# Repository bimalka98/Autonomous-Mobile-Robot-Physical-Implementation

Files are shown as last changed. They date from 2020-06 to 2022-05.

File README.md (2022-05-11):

## *Introduction*

This repository includes all the project files related to the development of an `Arduino based autonomous mobile robot`. The project is being done by a team of 5 undergraduates at the Department of Electronic and Telecommunication Engineering, University of Moratuwa, Sri Lanka. The following figures illustrates the `initial prototypes` of the planned mobile robot design and it may be subjected to various changes during the actual robot implementing stage due to possible reasons.

|*Version 1*|*Version 2*|
|:----:|:----:|
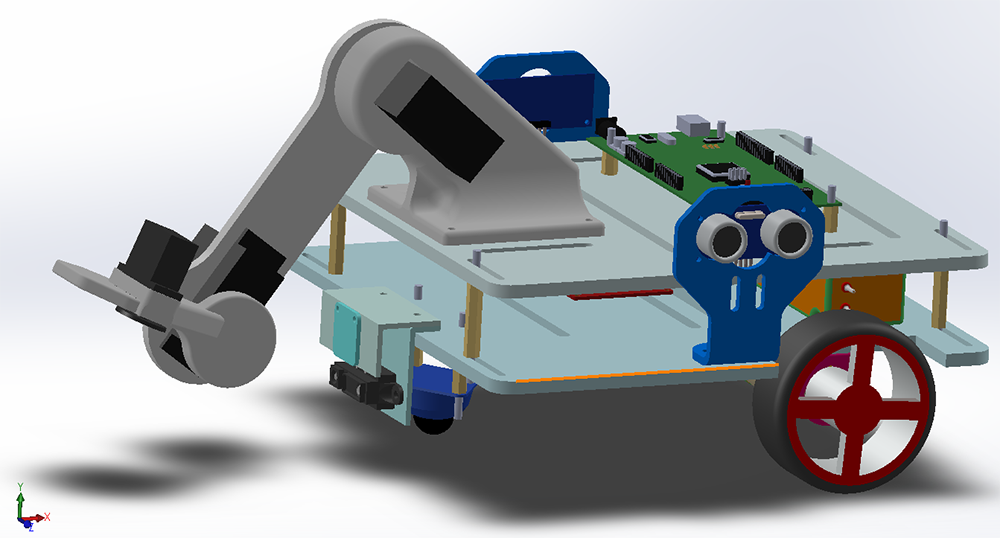
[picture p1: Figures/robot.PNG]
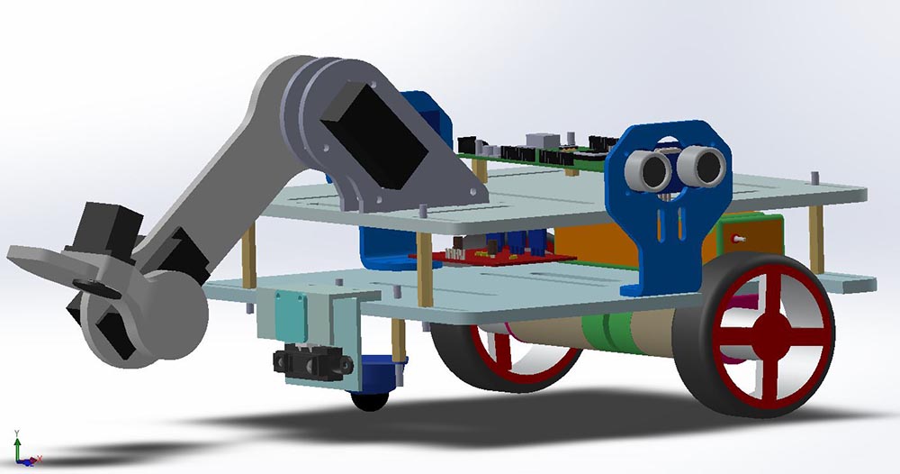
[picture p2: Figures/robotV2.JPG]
||  |

---

## *Current Status of the Project*

* Algorithms were developed.
* Working on coding.
* Physical Robot building stage was initialized.
* Robot arm's basic motion was implemented.
* Line following algirithm is being debugged.

---

## *Brief introduction about the files in repository*

### LatestStable
This folder contains the latest stable version of the Arduino code tested and debugged by the team.

### Arduino Sketches
This folder contains the most fundamental Arduino sketches for various sub-tasks encountered while designing the robot. Ex:
* Drive a Servo motor
* Drive a DC motor through L298N motor driver
* Drive a DC motor through VNH5019A Motor Driver-POLOLU
* Measuring distances using SharpIR

### SolidWorksModels
This folder contains all the SolidWorks models of the robot prototype.

### Laser Cut parts
DXF files of the parts which were laser cut to build the robot.

### 3D Print
STL files of the parts which were 3D printed to build the robot.

### ModifiedLibraries
Arduino libraries which were modified(or not modified) to suit to the given task.

### Documentation
`Documentation` folder includes some of the important documents related to the design of a mobile robot.

**ArduinoMega2560.pdf** : Information about `peripheral circuitry` of the ArduinoMega2560(Rev3).

**How to choose the correct servo.pdf** : Calculations to choose the correct servo motors for the given task.

**L298N Motor Driver Logical Functionality.pdf** : Underlying logical Functionality of the L2968N motor driver is shown by a truth table.

**Motor_selection.pdf** : Calculations required to determine the motor for the mobile robot are explained in this document.

**Power_source_selection.pdf** : Calculations required to choose the proper power source for the mobile robot are described in the document.

**Robot Mechanical Design.pdf** : The initial prototype of the mobile robot and the mechanical parts of the robot are explained in this document.

**Robot Sensors.pdf** : Sensors used in building the robot is described in this document in descriptive manner and drawbacks of other Sensors are also included.

**Subsumption Architecture.pdf** : A summary on the `Subsumption Architecture` is given in this document. It is a very robust  Control system Architecture which was introduced by R. A. Brooks of MIT in 1985.

---

# *Nothing Happens Over Night* 😈

> Great things are not done by impulse, but by a series of small things brought together. ~ Vincent Van Gogh

**Some of the moments of actual robot implementation...**

|Image| Description/ Comments|
|:----:|:----|
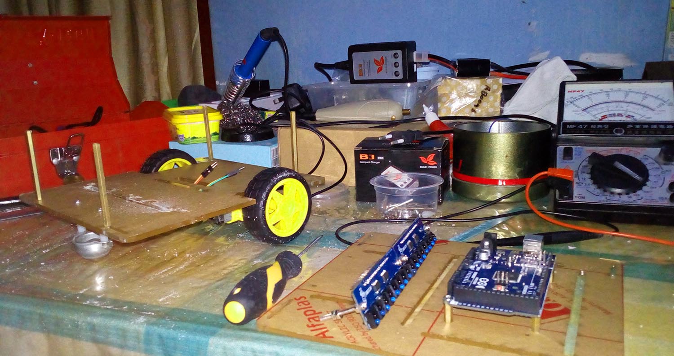
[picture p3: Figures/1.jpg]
|| *IR sensor Panel: 'Raykha S8' before mounting* |
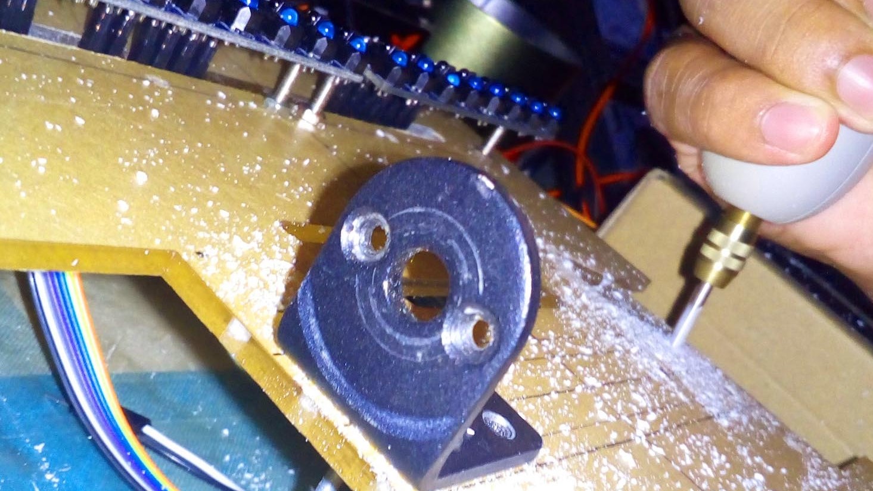
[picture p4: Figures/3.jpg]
|| *Drilling holes to mount motors* |
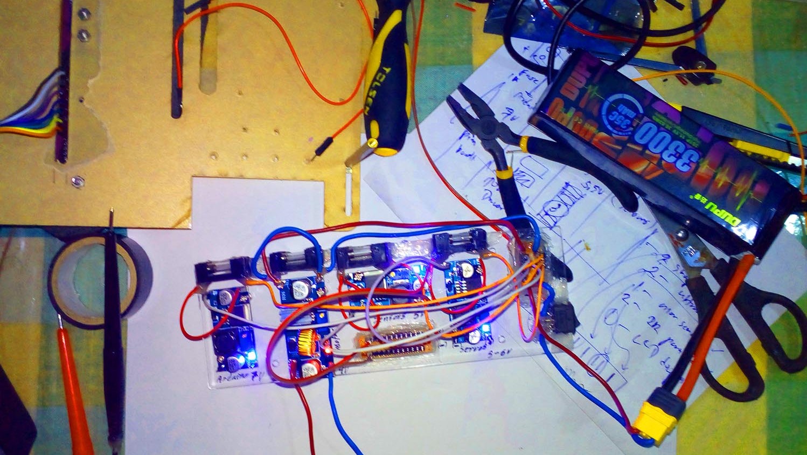
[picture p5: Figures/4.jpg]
|| *Checking the power distribution unit* |
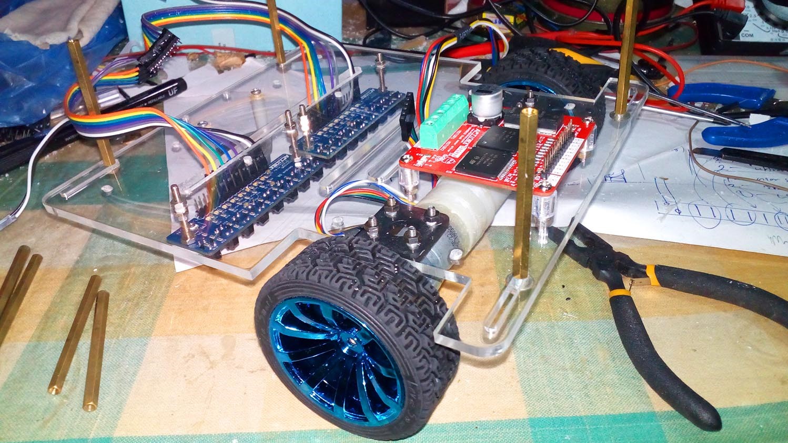
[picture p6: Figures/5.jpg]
|| *Mounting the motor driver: 'Dagaya 2.0'* |
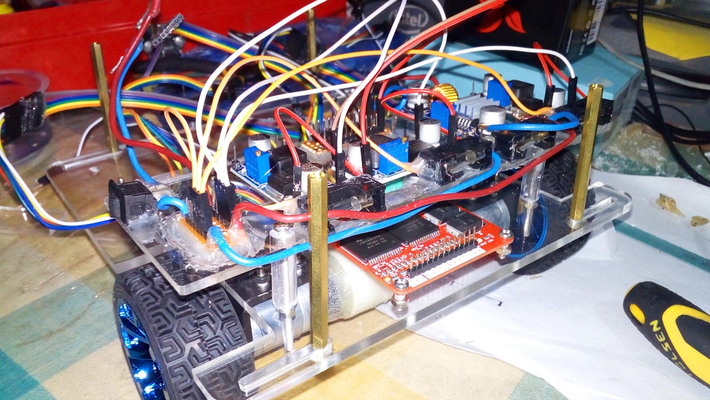
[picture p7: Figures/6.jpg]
|| *Mounting the power distribution unit* |
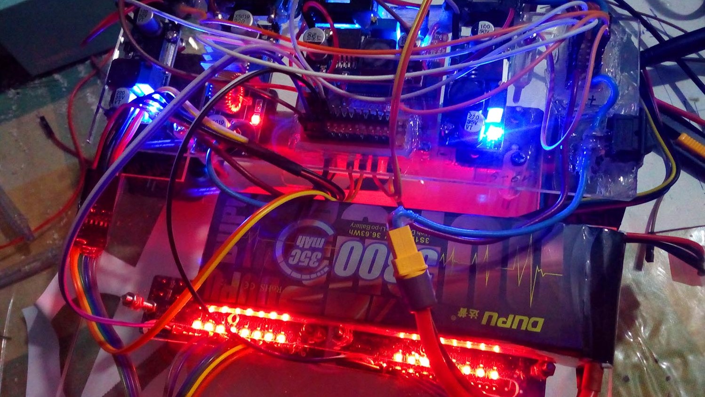
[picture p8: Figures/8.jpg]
|| *Powering up the IR sensor panels* |
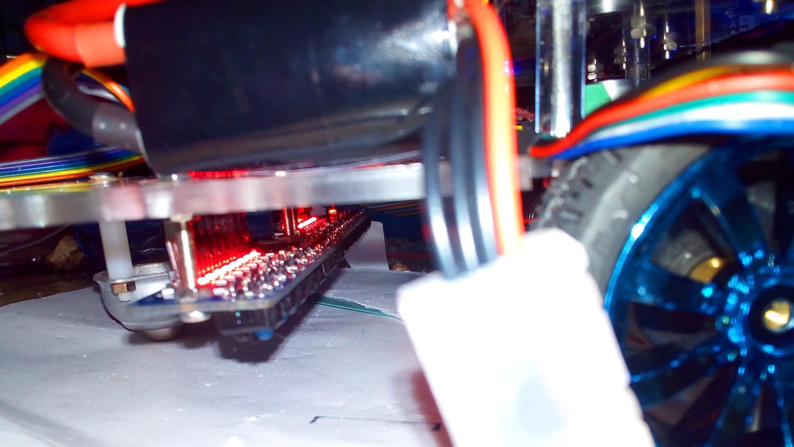
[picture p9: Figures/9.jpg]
|| *Powering up the IR sensor panels. Side View* |
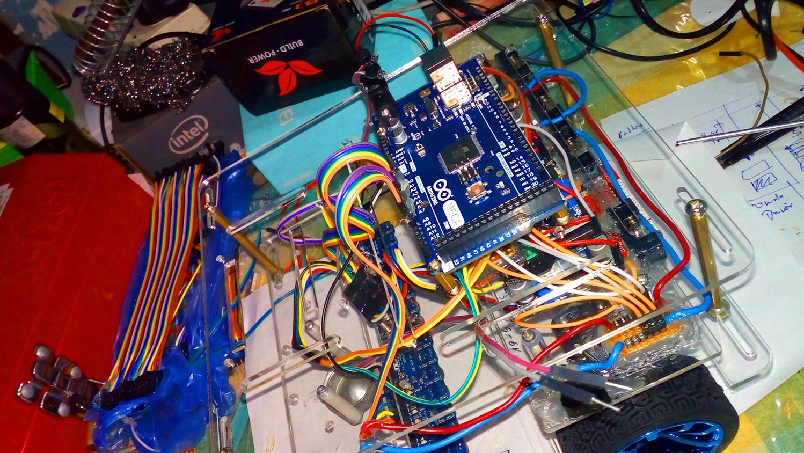
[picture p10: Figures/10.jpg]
||  *Mounting the robot brain. ArduinoMega2560* |
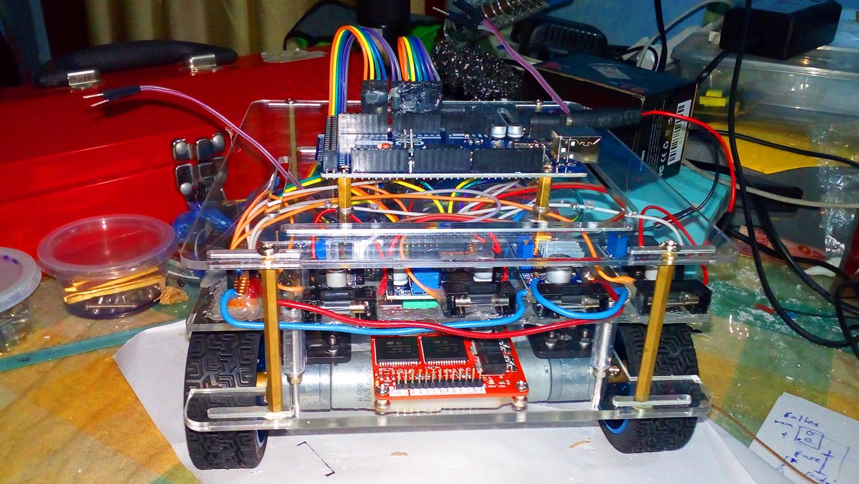
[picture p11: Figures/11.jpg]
||  *Back view* |
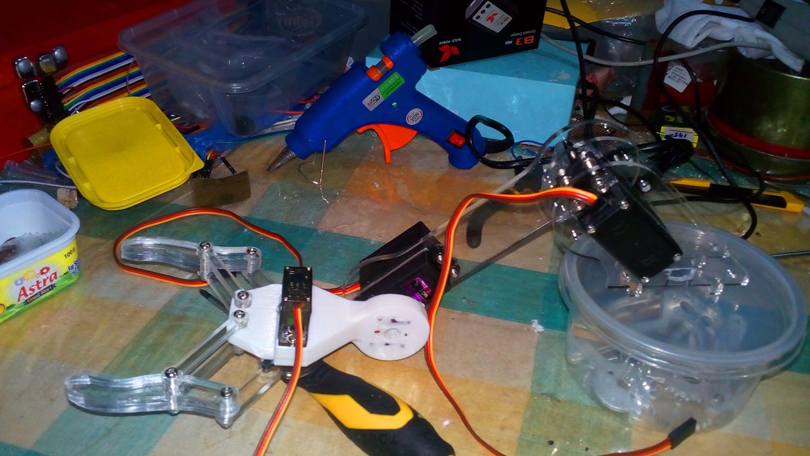
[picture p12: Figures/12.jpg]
||  *Making the robot arm* |
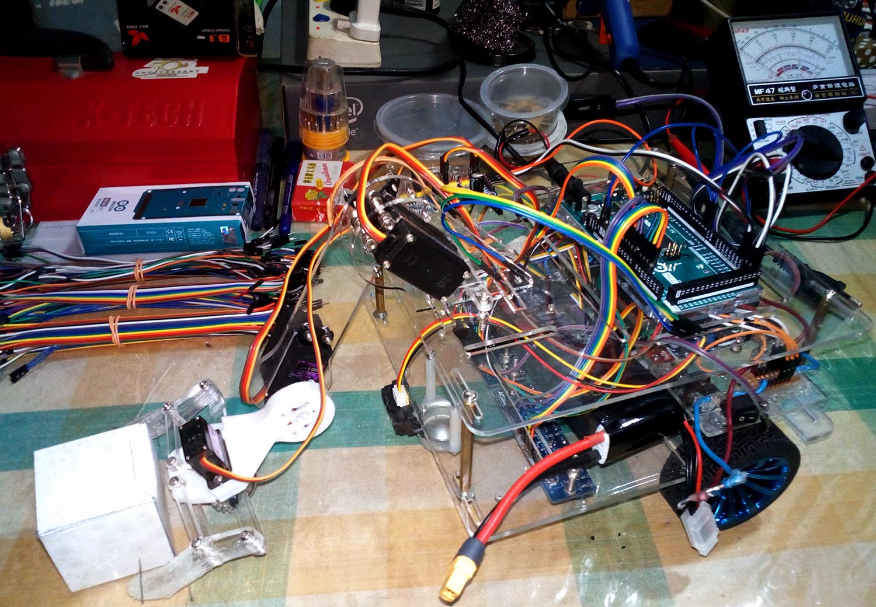
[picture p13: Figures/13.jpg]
||  *Robot up to now* |

---

## *Team*

> *Individual commitment to a group effort* --that is what makes a team work, a company work, a society work, a civilization work. ~ Vince Lombardi

#### *Team leader*
[Thalagala B.P.](https://bimalka98.github.io/)

#### *Team members*
1. [Sandeepa H.K.C.A](https://github.com/AvishkaSandeepa)
2. [Hewavitharana D.R.](https://github.com/Hevidra)
3. [Nagasinghe K.R.Y.](https://github.com/Ravindu-Yasas-Nagasinghe)
4. [Kumarasinghe H.A.N.H.](https://github.com/nikeshi99)

## *Additional Notes*

*The [Webots](https://cyberbotics.com/) robot simulator implementation of this Robot can be found at [`webots-Autonomous-Mobile-Robot`](https://github.com/bimalka98/Autonomous-Mobile-Robot-Webots-Simulation).*

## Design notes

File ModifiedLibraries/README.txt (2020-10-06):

Keep all the modified libraries in the following directory: 

Instead of ASUS there will be your user name

****************************************************
C:\Users\ASUS\Documents\Arduino\libraries\
****************************************************

If you need to modify any library, modify the libraries in the given directory. Otherwise sketches do not work properly.

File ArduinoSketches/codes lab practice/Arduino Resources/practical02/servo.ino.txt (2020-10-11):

#include <Servo.h> 
 
Servo myservo;  
// create servo object to control a servo 
// twelve servo objects can be created on most boards 
 
int pos = 0;    // variable to store the servo position 
 
void setup() { 
  myservo.attach(9);  // attaches the servo on pin 9 to the servo object 
} 
 
void loop() { 

  for (pos = 0; pos <= 180; pos += 1) { 
    // goes from 0 degrees to 180 degrees 
    // in steps of 1 degree     
    myservo.write(pos);              
    // tell servo to go to position in variable 'pos'     
    delay(15);                       
    // waits 15ms for the servo to reach the position 
  } 
  for (pos = 180; pos >= 0; pos -= 1) { 
    // goes from 180 degrees to 0 degrees     
    myservo.write(pos);              
    // tell servo to go to position in variable 'pos'     
    delay(15);                       
    // waits 15ms for the servo to reach the position 
  } 
}

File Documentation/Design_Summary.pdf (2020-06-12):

EN2532 - Robot Design and Competition

# Project Proposal

Group : BRAND | 180631J . 180564F . 180241M . 180411K . 180337M
| Submitted on June 13, 2020

## Overall Strategy

The overall task is subdivided into several sub tasks and they are executed one after the other where each sub-task can be considered as a function which will be called inside the main function of the control system. When one sub-task is over the control of the robot is handed over to the next sub-task. That is if robot starts misbehave in the middle of a task we have to start again from the very beginning.

- Proportional and derivative control schemes that is PD algorithm is used to follow the line using an IR sensor panel designed in a special arrangement using 8 IR sensors.
- Alternate Wall following part is also controlled by a similar PD algorithm and ultrasonic sensors are used for this as the task is not time critical.
- In order to follow circular paths differential drive algorithm is used.
- To identify the color of the bottom surface of the box we planned to use a robot arm of single degree of freedom with respect to its base with an attached gripper mechanism and a color sensor placed in front of the robot. The method will be explained in the algorithm section.

## Robot Hardware Design

We used solid works as CAD 3D modeling software. After considering dimensions and weight of the all component we came up with our robot hardware design. All the component including PCB, sensors were drawn separately according to their actual/(approximated) dimensions and connected all together. There are 3 main parts in robot design as robot arm, lower platform, and upper platform. Robot arm will be made through 3D printing and platforms where all the components are mounted will be made by using Acrylic Plexiglases as we need strong and protective structure to hold each component. And other components like sensor holders are also going to made with Acrylic.

## Sensors

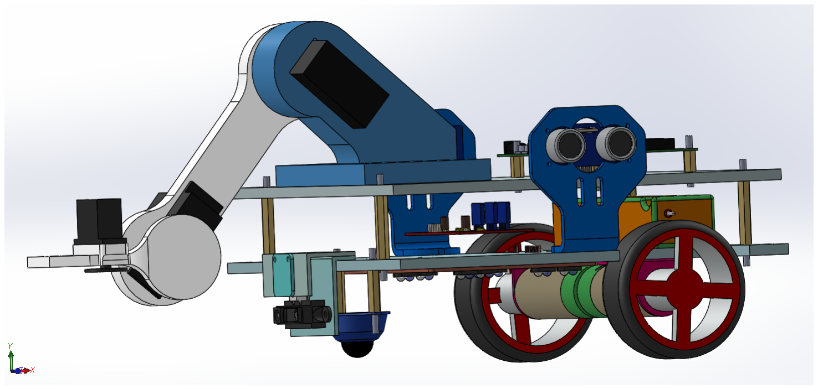
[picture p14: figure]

Purpose | Sensor
Line Following | A sensor panel of 8 TCRT5000 IR Sensors
Wall Following | Two HC-SR04 Ultrasonic Sensors
Box detection | GP2Y0A21YK0F Sharp IR sensor
Gate detection | GP2Y0A21YK0F Sharp IR sensor
Color detection | TCS34725 - Color Sensor

Table 1: Used sensors in the design

1

## Algorithms

For every sub task there is a unique algorithm to achieve the robot behavior of that particular sub-task. Within these algorithms the most basic controlling algorithms such as line following PD algorithm, motor driving algorithm, are combined together with the other unique algorithms to obtain the desired robot behavior. All the algorithms can be found at https://dms.uom.lk/s/3tqCf5aXDzK9eZZ and was not included here as it consumes a lot of space.

## Actuators

Purpose | Actuator | Quantity
Motors for wheels | Pololu Metal Gear motor 25Dx67L mm | 2
HP 12V with 48 CPR Encoder
Robot arm | TowerPro MG996R servo motors | 2
Gripper Mechanism | TowerPro MG90S servo motor | 1

Table 2: Used actuators in the design

L298N motor driver will be used to control the motors while PCA9685 servo driver multiplexer which can drive up to 16 servos simultaneously will be used to control the servos in robot arm.

## Power

We selected XK Detect X380 11.1V 3S 5400mAh Lipo battery as the power source for our robot. The voltage of battery is taken by determining the maximum voltage required which is 9V for for the motors. Capacity is determined by the total current required at the worst case scenario which is 9000mA and the time of running the robot which is 0.5h. The required minimum discharge rate is 1.667C. The discharging rate of this battery is 20C so it is more than enough. Some of the main advantages of using this Lipo battery are high energy density, high discharge rate and no memory effect.

## Processing Unit

In our design there is only a centralized processing unit and therefore all the required data processing and calculations are done there. We have decided to use Arduino MEGA2560 board which is an open source development board based on ATMEGA2560 microcontroller. Programming of the bard is done through ARDUINO IDE. We have chosen this because it has ample of analog and digital input/output ports with several PWM supported digital pins, which are basic requirement in this robot implementation.

## Task Delegation

Up to now only the algorithms are developed independently as given in the table and tasks related to initial stage of actual robot building such as hardware model designing were done by all the members together and therefore there was no specific task delegation. In addition to that task like PCB designing and real hardware design is not allocated to anyone yet.

Name | Index | Allocated Tasks
Sandeepa H.K.C.A | 180564F | Line Following algorithm , Wall Following Algorithm
Hewavitharana D.R. | 180241M | Algorithm related to the robot behavior in circular maze area
Thalagala B.P. | 180631J | Robot arm design and its controlling algorithm
Nagasinghe K.R.Y. | 180411K | Algorithm related to the robot behavior in Ramp area
Kumarasinghe H.A.N.H | 180337M | Algorithm related to the robot behavior in gate area

Table 3: Task delegation among team members

2

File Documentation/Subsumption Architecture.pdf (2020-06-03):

## A summary on ‘A robust layered control system for a mobile robot’ by R. A. Brooks(1985), AI Laboratory, MIT

Thalagala B.P. 180631J

April 30, 2020

When implementing an autonomous intelligent mobile robot there are several requirements to be fulfilled by the control system of the robot and there are different approaches to fulfill those requirements.

Requirements of a control system[1],

1. A Robot Probably has multiple goals which may have varying priorities depending on the context at the moment, therefore control system must be able to identify the situation of environment and give the priority to what is necessary while providing required services to the low level objectives.
2. A robot has multiple sensors which in nature has some error in their readings comparison to the real physical quantities that are measured. Therefore control system must be able to model the environment as much as accurate by using available sensor data wisely.
3. The robot must have some robustness. For that the control system must be able to drive the robot with some performance by using available sensor data even though one or more sensors are not in proper working condition.
4. The processing power of the control system must be able to be increased in case of adding more components to the robot in order to increase its capabilities . This feature is known as additivity of the control system.

The underlying process of most of the approaches in fulfilling these requirements has three basic steps.

Problem is decomposed into several sub-problems
↓
Sub-problems are solved
↓
Solutions to sub-problems are composed together to make up the final solution

Depending on the way of decomposing the problem(at the first step), the architecture of control system of the mobile robot differs. The conventional method is known as Sense-Plan-Act (SPA) Architecture. Here the problem is decomposed into functional
modules | depending | on | the | internal | workings
of the solution.This is regarded as a horizontal decomposition of the problem into vertical slices[1].

The overall function of this kind of control system is, taking information from the environment using sensors, planing the actions need to be taken and finally executing the planned tasks using actuators.The sub problems of SPA architecture can be shown as follows.

Sensors ↓

Perception
Modeling
Planning

Task Execution
Motor Control

↓

Actuators

Figure 1: Sense-Plan-Act (SPA) Architecture

All the sub-problems need to be solved to a certain extent and composed together essentially, before testing a mobile robot designed under this category. Implementing a solution for only one sub-problem is not sufficient to operate the robot with any amount of performance.

In addition to that changes in control system cannot be done considering only one sub-problem(a piece in above figure) alone. That is if some change in a piece is needed, either we have to keep the interfaces to adjacent pieces unaltered or do the necessary changes of the functions in adjacent pieces.
Note: From this point onward most of the information will be directly related to the mobile robot made by Rodney A. Brooks in 1985, at Artificial Intelligence Laboratory, MIT. Therefore not general.

## Subsumption Architecture

In Subsumption Architecture[1] the problem is decomposed based on the desired external actions of the mobile robot.This is regarded as a vertical decomposition of the problem into horizontal slices[1].

Sensors →

Reason about behavior of Objects Plan changes to the World
Identity objects
Monitor Changes
Build Maps
Explore
wander
Avoid Objects

→ Actuators

Figure 2: Subsumption Architecture

To understand this architecture there are some concepts to be identified at first,

Levels of competence

A level of competence describes a specific set of behaviors which the robot should have over all the environments that it will deal with.When the level of competence increases even more specific behaviors and additional constraints are added to get the desired final robot behavior. This can be viewed as follows and notice that a particular lower level competence is included in the immediate higher level.

Level | Behavior
0 | Avoid contact with objects
1 | Move leisurely in the environment without
hitting objects
2 | Explore the reachable environment
3 | Build maps of the environment and plan
routes from one place to another
4 Become aware of the changes in ‘static’ environment
5 Understand objects in current environment and perform task related to specified objects
6 | Create and execute plans
7 | Understand behavior of objects in environment
and modify plans accordingly

Layers of Control

In this subsumption architecture[1], sub-control systems can be built corresponding to each level of competence and they are able to operate individually. These sub-control systems are called as control layers (zeroth level, first level, . . .).

Particular lower layer is not aware about its upper layer which sometimes inject necessary data to the lower layer to limit the normal flow of data in lower layer to achieve desired robot behavior. And the level of competence can be increased to the next level by adding a new control layer on top of the existing layers.

The most interesting thing about this architecture is that it naturally takes care of the requirements which were discussed at the beginning, that an autonomous mobile robot control system should fulfill.

1. Multiple goals: As layers are able to work independently on multiple goals at the same time, there is no need of specifying what goal should be pursued by the robot since every goal is being pursued to a certain extent at a given moment and information given by all the layers can be used to take one final decision to be executed.
2. Multiple Sensors: Since data form all sensors are available for each control layer and it is allowed to process the data in the way it wants to achieve its goal, there is no need of sending all the sensor data to a central processor to process.
3. Robustness: Since a higher control layer is added only after its immediate lower layer is well debugged and tested in the environment, although there is any failure of operation in one layer, all the layers below that layer are continue to work, with the highest level of competence which corresponds to the working layer. Therefore robustness is naturally there in this architecture.
4. Aditivity: Through allocating a processor for each control layer, the processing power of the robot can be increased whenever we want. All we have to do is when we adding a new higher level control layer use a dedicated processor for that layer.

Structure of Layers

In this architecture we do not need to consider all the inputs, all the objectives and all the behaviors within a single decomposition. Because we can decompose each layer in a different way to take out the maximum performance. In addition to that each layer is made up of several small asynchronous processors(refer as modules) which sends and receives messages from other modules, without any central control or any global memory. Moreover Inputs and outputs of the modules can be limited by other modules by sending messages. (This is the main concept behind including lower layers inside the higher layers.)

## Robot Control System Instance for Subsumption Architecture

Zeroth Layer

Zeroth or the lowest layer of the mobile robot control system is designed to achieve level zero competence. That is this control layer makes sure that the robot does not make any contact with objects in the environment either moving or stationary.

I. If it is a stationary object and the robot is going to hit it, modules command the robot to stop where it is.

II. If some object is moving towards the robot, modules command the robot to move away from that object.

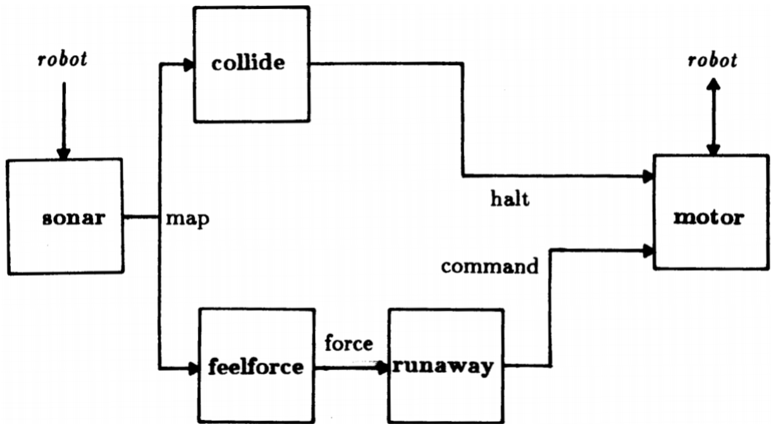
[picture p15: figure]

Figure 3: Modules and their interconnection in the zeroth layer[1]

Purpose of each module briefly, can be given as follows.

- Sonar Module has three sub functions as, taking sonar readings, check their validity and filter out invalid readings and build a robot centered map in polar coordinate system.
- Collide Module inspects the map produced by the sonar module and if a stationary object is detected which is on the way of robot, it sends a message through the halt line to the motor module.
- Motor Module accepts commands related to the motion of robot(for angular motion - angle and angular velocity(speed of turn)/for linear motion - distance to be traveled and velocity) and converts them into electrical signals which can then be executed by actuators. If a halt signal receives, it will be prioritized over any other received signals.
- Feelforce | Module | also | inspects | the
map produced by the sonar module and associates(maps) every detected object to a corresponding repulsive (drive back) force and produce a resultant force considering every such force.

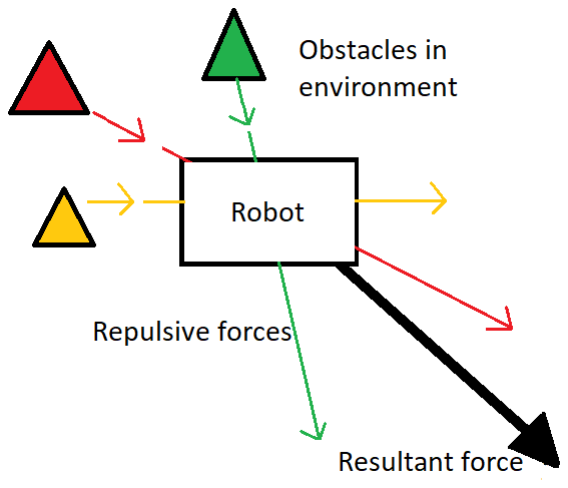
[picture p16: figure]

Figure 4: Determination of feelforce

- Runaway Module observes the resultant repulsive force produced by the feelforce module and sends necessary commands to the motor module.

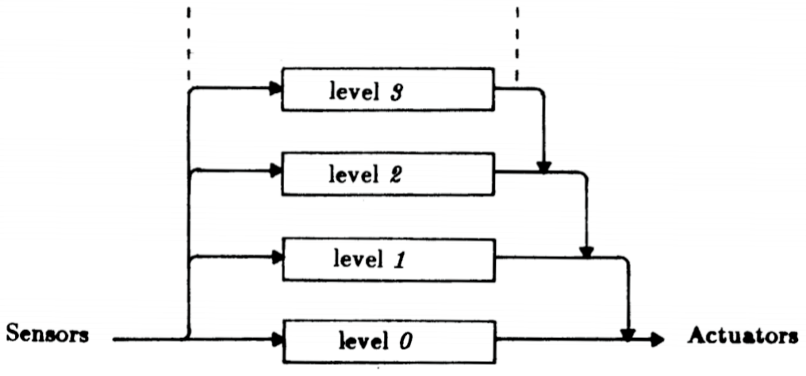
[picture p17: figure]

Figure 5: Layered Control System[1]

After building the zeroth level of the control system, which was made to achieve level zero competence, the robot is tested in the environment and then it is fully debugged. Then that layer in the control system will never be altered. All the other higher level layers are built on top of this layer. Higher layers are allowed to take data from lower layers and also permitted to inject necessary information to the lower layer modules. This can be represented as follows.

First layer

First layer with the aid of the zeroth layer achieves the level one competence.That is these layers together make sure that the robot moves leisurely without making any contact with either stationary or moving objects in the environment.

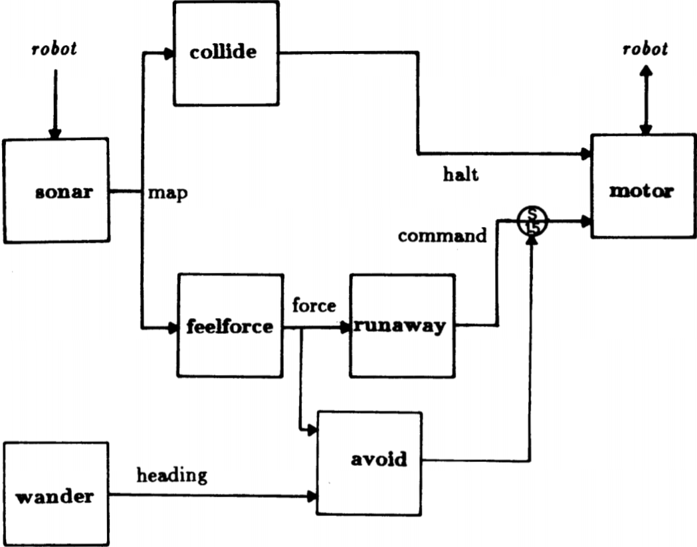
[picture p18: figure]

Figure 6: Interconnection between first layer modules with existing zeroth layer[1]

- Wander Module randomly chooses a direction repeatedly at every given amount of time to move.
- Avoid Module takes (1)the suggested direction from the wander module and (2)direction of the resultant repulsive force from the feelforce module in the zeroth layer, into account and then decides a direction to move. This new direction is then injected to the output line of the runaway by suppressing the normal data flow of that module.

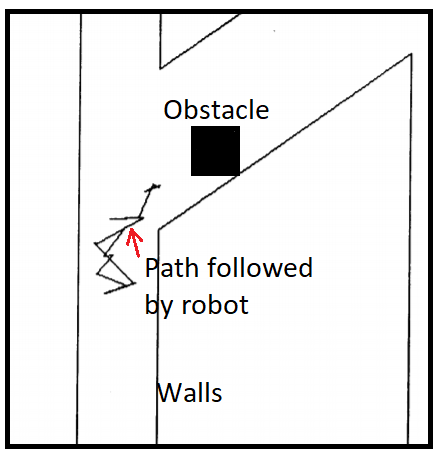
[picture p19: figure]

Figure 7: The path followed by the robot after implementing layer one and zero of the control system with level one competence(a simulation result)[1]

## Conclusions

- Subsumption architecture introduces a way of decomposing the problem depending on the desired robot’s behavior whereas in SPA architecture it is done by considering the internal workings(sensing/Modeling/planning/...) of the control system of the mobile robot.
- This architecture allows us to build complex robot control systems step by step, so there is no need of considering the whole problem at once to initiate the building of control system.
- Control of the system is not centralized and it is divided among several asynchronous processors which try to do their best individually so that all the goals are pursued to a certain extent.

## Bibliography

[1] R. A. Brooks. | A robust layered control
system | for | a | mobile | robot. | Artificial
Intelligent | Memo-864,Artificial | Intelligence
Lab,Massachusetts | Institute | of | Technology,
September 1985.

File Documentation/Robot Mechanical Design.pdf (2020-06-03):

Department of Electronic and Telecommunication Engineering

## University of Moratuwa, Sri Lanka

EN2532 - Robot Design and Competition

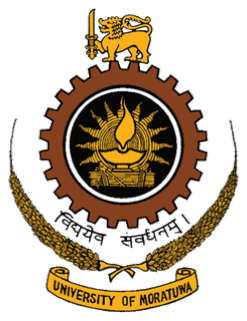
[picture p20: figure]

# ROBOT MECHANICAL DESIGN

Submitted by

Thalagala B.P.

Sandeepa H.K.C.A

Hewavitharana D.R.

Nagasinghe K.R.Y.

Kumarasinghe H.A.N.H

180631J

180564F

180241M

180411K

180337M

Submitted on

## April 17, 2020

## Initial Prototype of the Mobile Robot

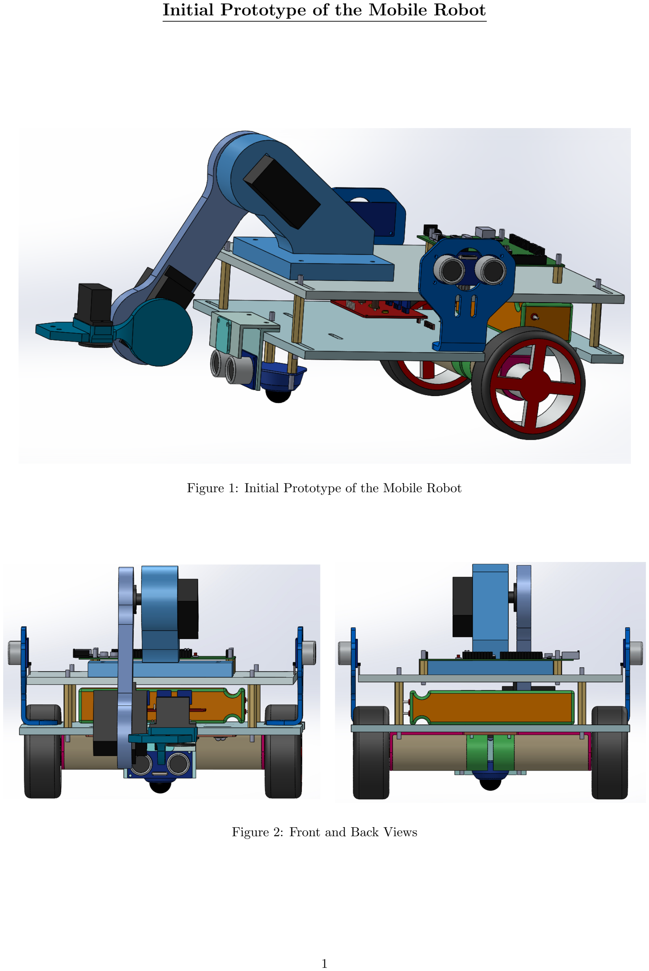
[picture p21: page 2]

Figure 1: Initial Prototype of the Mobile Robot

Figure 2: Front and Back Views

## Explanation for each Component or Mechanism

Robot arm

Robot arm is used to lift the box which robot has to inspect the colors of front and bottom sides. The arm is made of plastic to reduce the overall weight and to facilitate for the servo motors which are not capable of lifting a huge weight because of their less torque. In addition to the parts shown in figure there will be a gripper mechanism in front of the arm to hold the box.

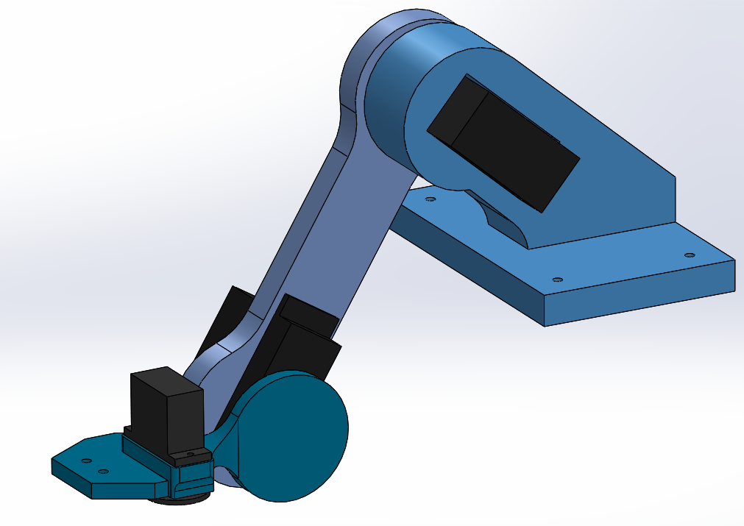
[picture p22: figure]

Figure 3: Robot arm

Platforms

Platform is the part where all the sensors, micro controllers, actuators and every other components including mechanisms like robot arm are attached. Therefor it should be made of strong materials such as wood, metal or Acrylic Plexiglas which is widely used in making small robot chassis.

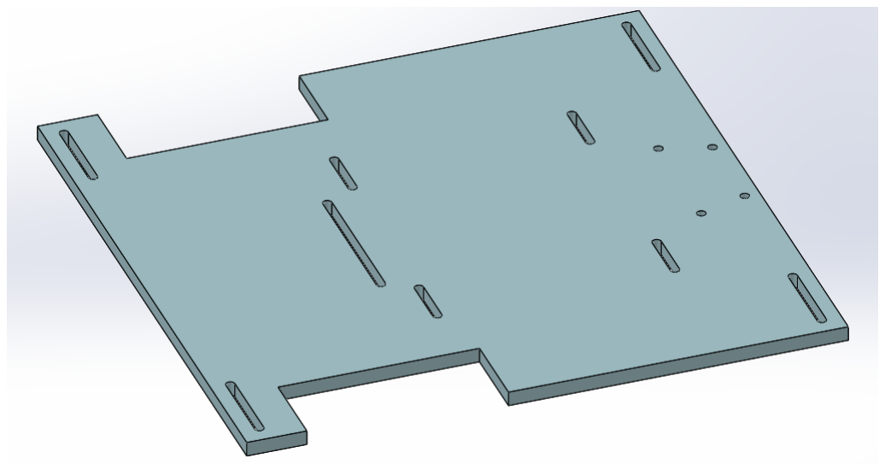
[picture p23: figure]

Figure 4: Lower platform

In our robot there are two platforms, one top of the other to facilitate all the necessary components nicely otherwise robot will be a real mess because of not having enough space to attache all the required components.

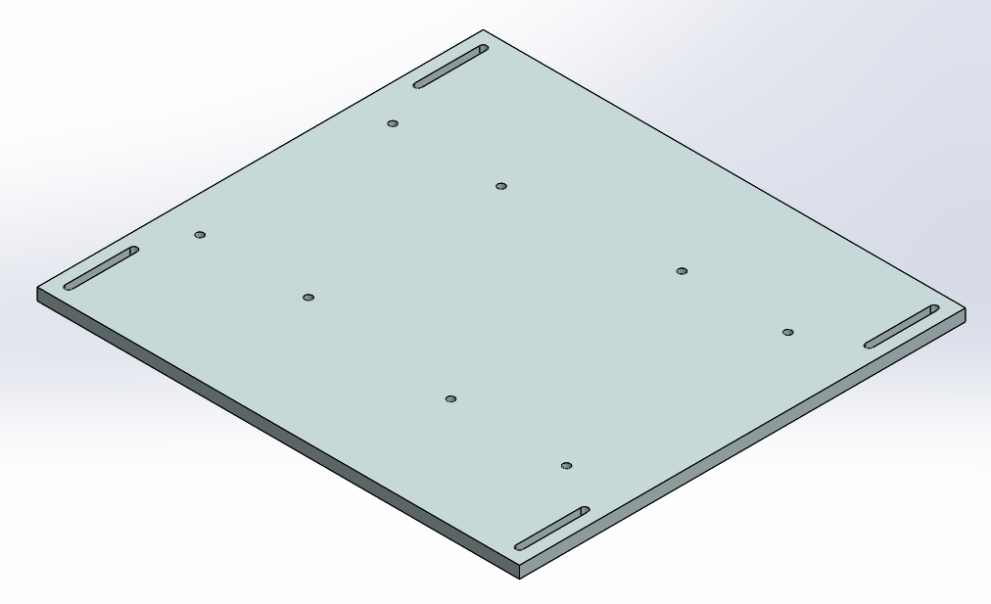
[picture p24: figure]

Figure 5: Upper platform

Spacers

Spacers are mainly used to make the gaps between upper and lower platforms. In addition to that spacers with low height are used to maintain the distance between platform and the PCB s.

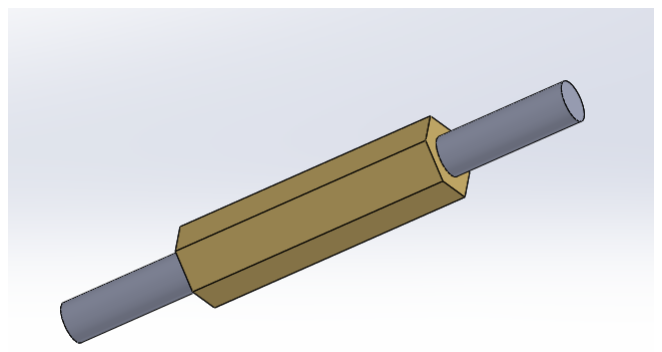
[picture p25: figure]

Figure 6: Model of a common brass Spacer

Arduino Mega 2560 Board

Arduino board is used as a open-source microcontroller board. It is based on Atmega 2560 microcontroller. This is used as robot brain. It takes environmental information and process these details and gives resultant output which programmer says. In short it is used to control the other components of the robot. it has its own 5V and 3.3V outputs so they can also use as input for other components.

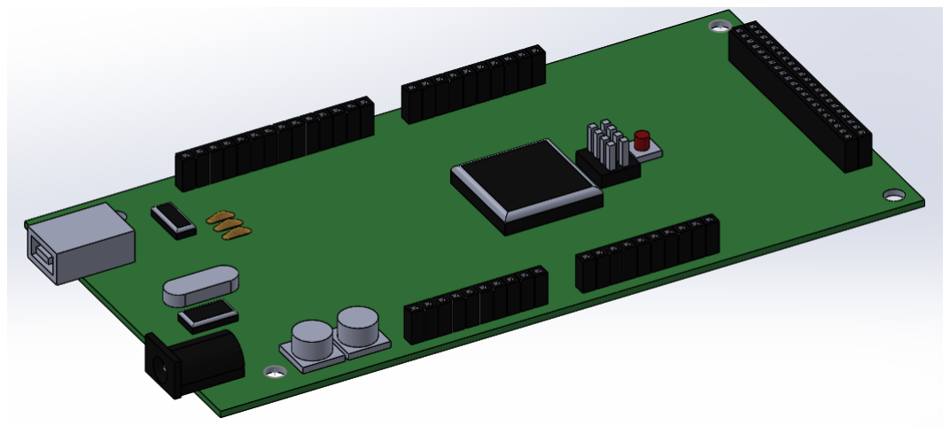
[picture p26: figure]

Figure 7: Model of the Arduino Mega Board

HC-SR04 Ultrasonic Sensor

This is an ultrasonic sensor, also known as an ultrasonic transducer that is based on a transmitter and receiver and mainly used to determine the distance from the target object. In our case, we use this sensor to detect distance to the colored box and distance to the walls in wall following part.

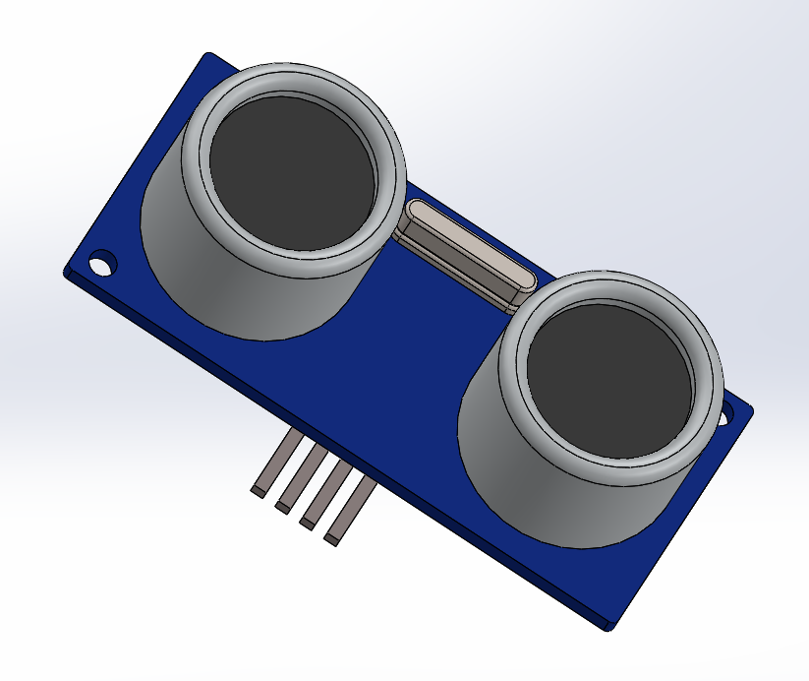
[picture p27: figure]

Figure 8: Model of an Ultrasonic Sensor

So, we have to use three ultrasonic sensors for achieve this task. Two sensors are attached on the left and right sides of the robot to detect the distance to the wall following part. One sensor is attached to detect the distance to the box. It mainly depends on the sound waves working on “non-contact” technology. The required distance of the target object is measured without any damage, giving accurate and precise details.

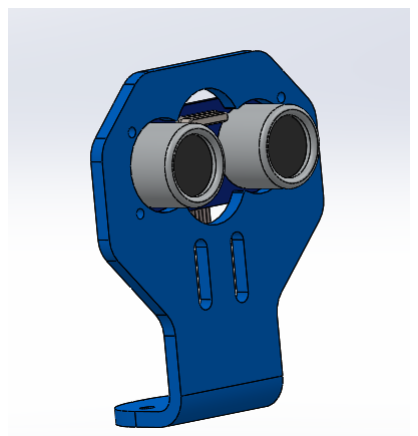
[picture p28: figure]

Figure 9: Ultrasonic sensor and its holder

TCS34725 RGB sensor

The high sensitivity, wide dynamic range, and IR blocking filter make the TCS3472 an ideal color sensor solution for use under varying lighting conditions and through attenuating materials. We use this to detect the colour of the box which is placed in the middle of a line segment which is a radius of the circle.

Figure 10: Model of the Color Sensor

Senser Holders

Sensor holders are used to attach sensors to the main platform whenever it is not possible to obtain the desired inputs by directly attaching them to the platform. Holes are there to attach the holders in front of the lower platform.

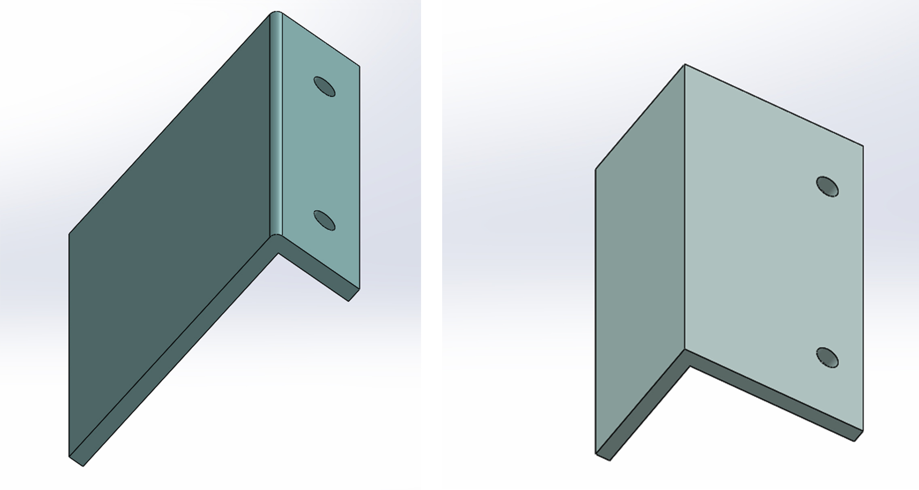
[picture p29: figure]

Figure 11: Front ultrasonic sensor holder(left) and color sensor holder(right)

IR Sensor Panel

This sensor is categorized as reflective sensor. In this module both emitter and photo-transistor are packed as a package. This sensor is used to detect presence or absence of a reflective object or to identify the line. Mostly it is used to detect lines for line following robots. In our robot, this sensor is also used as line detector.

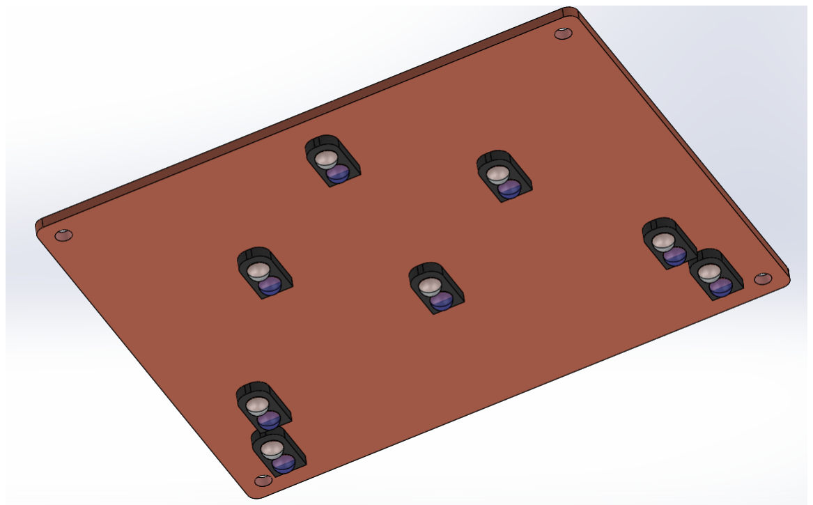
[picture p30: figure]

Figure 12: Model of the IR sensor panel

Gear Motors

We are asked to use two metal motors with following features for the robot as they are provided by the university.

- 25D Pololu metal gear motors
- 12V high power
- 48 CPR Encoder
- 34:1 Gear ratio

Gear motors are used to supply the necessary rotary motion to wheels. The quadrature encoders in this motor can be used to add speed and position feedback to our metal gear motors. We use these encoders to find the number of turns the wheel has turned, so we can find the distance traveled by the robot.

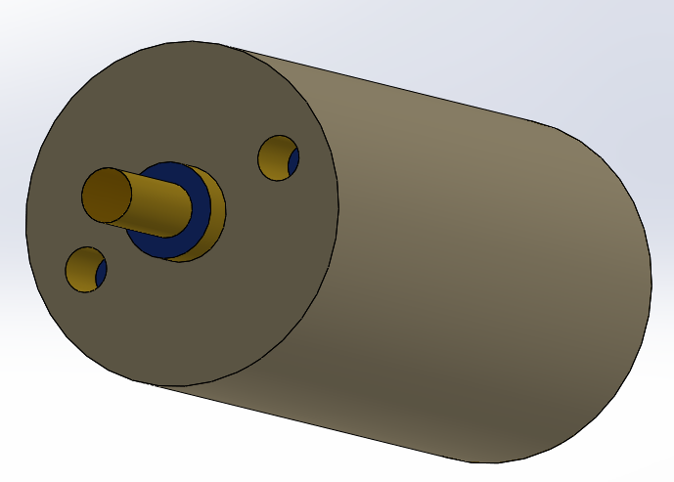
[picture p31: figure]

Figure 13: Model of the 25D Pololu Metal gear motor

Wheels

We use two robot wheels with dimensions of diameter 6.5 cm and width 2.5 cm. In our project we are expecting to use plastic rims. We are hoping to use semi pneumatic wheels as it holds its shape with combination of air and strength of side walls. We use the flat wheels as their grip is high so we can maintain the balance of the robot even when it is going on the ramp.

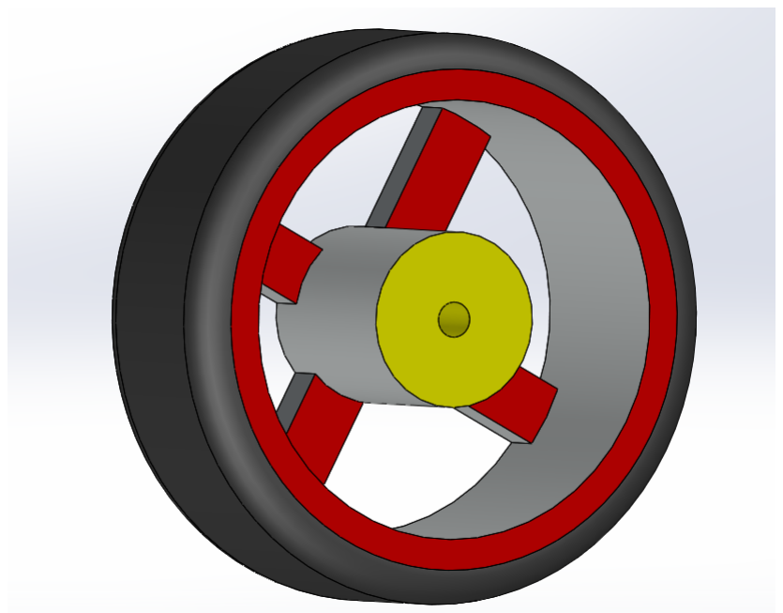
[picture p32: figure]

Figure 14: Model of the Wheel

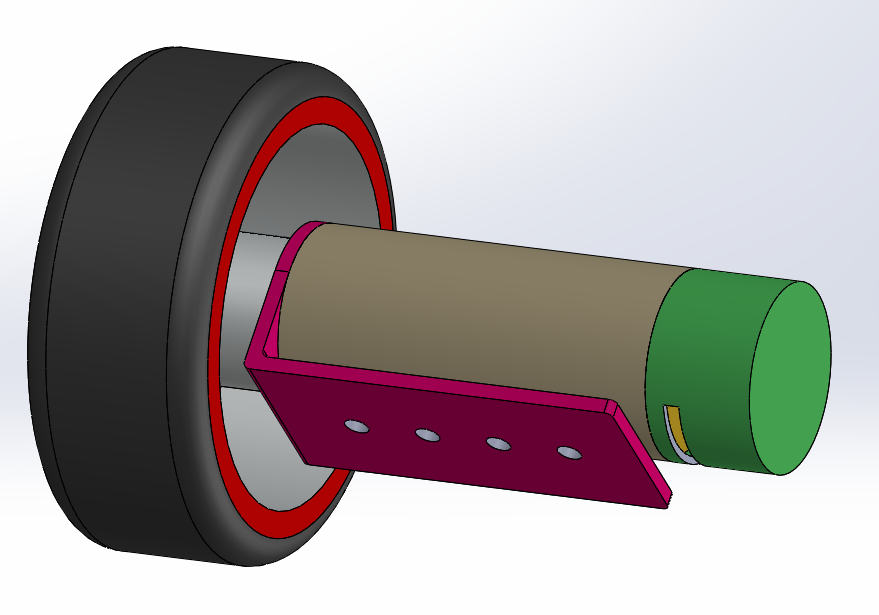
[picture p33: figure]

Figure 15: Model of the Assembled Wheel, Motor, its holder and the guard for Encoder(Green color part)

Power Supply Unit

The battery acts like the heart of robot. Because it empowers all electrical parts of the robot. Different components of the robot require different voltages. But we only use one battery unit for that.Therefore, the main voltage should be distributed to different voltages as needed for each component. (Such as 12V in to 9V, 6V, 5V, and 3V). To accomplish this task, we use the power supply units (Power distribution circuit).

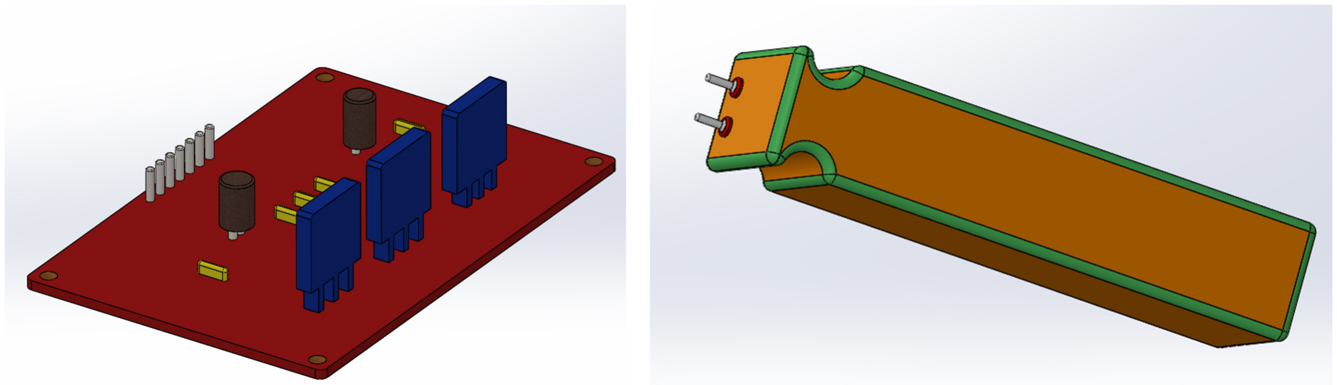
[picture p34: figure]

Figure 16: Model of the Power distribution Circuit and Battery

Caster Wheel

A caster is an undriven, single, double, or compound wheel that is designed to be attached to the bottom of a larger object to enable that object to be moved. There are two types of caster wheels as wheel and ball caster. We use the ball caster as it has much more agility than wheel caster. Its purpose is to act as a great third contact points for small robots.

Figure 17: Model of the Caster Wheel

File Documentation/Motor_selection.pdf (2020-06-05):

# Motor Selection

Group : BRAND | 180631J . 180564F . 180241M . 180411K . 180337M
| Submitted on May 7, 2020)

## 1 What is a DC motor?

A DC motor is a mechanically commutated electric motor powered by “direct current”. This converts direct current electrical energy into mechanical energy. There are two main types of DC motor based on existing commutating mechanism. They are brush DC motors and Brushless DC motors. These motors are comprised of six main components; permanent magnets, a spinning armature called a rotor, an axle, a commutator, field magnets, and brushes (optional). Using magnetism, they can create rotational motion.

## 2 Calculations

Note: For all the calculations the weight of the robot is approximated as 1.8 Kg while velocity of the robot is decided to be nearly 0.21 meters per second depending on some critical parameters.

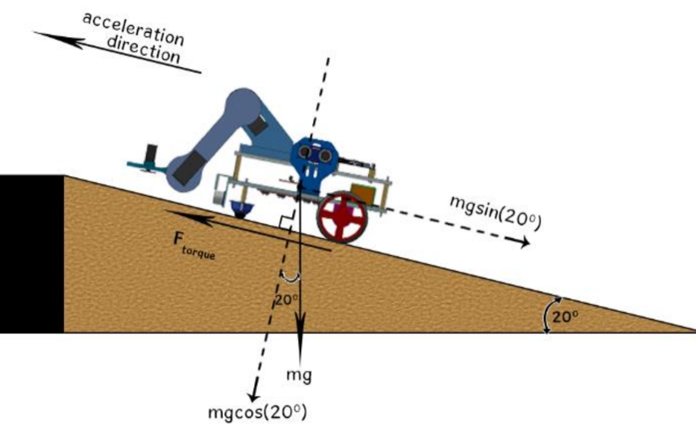
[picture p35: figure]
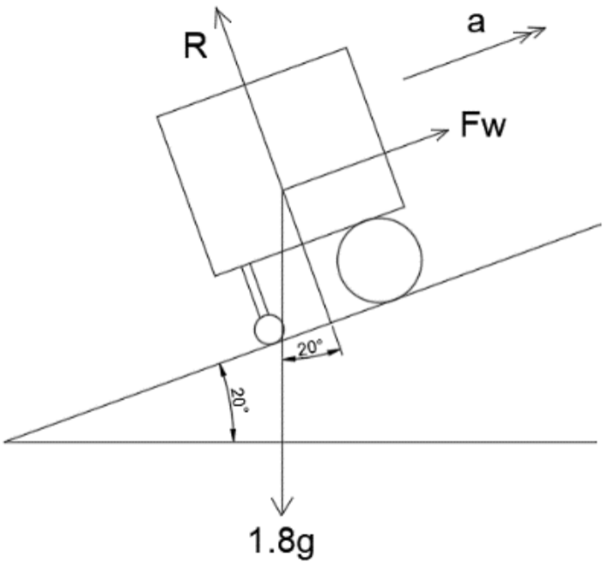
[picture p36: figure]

(a) (b)

Figure 1: Free force Diagram of the mobile robot in the Ramp Area

Let’s assume we need to achieve maximum velocity within 1s,

v = u + a ∗ t
0.12 = 0 + a ∗ (0)
a = 0.12ms⁻¹

Assume that there is no friction between the robot and surface.

F = ma
FW − mg ∗ sin(20) = ma
FW = m ∗ (a + g ∗ sin(20))
FW = 1.8 ∗ (0.12 + 9.8sinn(20))

FW = 6.2492 N

Torque needed from both motors,

τ = FW ∗ r
= 3.25 ∗ 6.2492 ∗ 10⁻²

= 0.203 Nm

Therefore torque required from both of the motors, τ = 28.7472 oz − in, Torque required from one motor τ = 14.3736 oz − in

Revolutions Per Minute(rpm) of the motor,

rpm =

0.12ms⁻¹ ∗ 60
2π ∗ r

=

0.12ms⁻¹ ∗ 60
2π ∗ 3.25 ∗ 10⁻²
= 35.2589 rev.min⁻¹

Angular velocity of motor,

ω = 35.2589 rev.min⁻¹
∗

2 ∗ π
60
= 3.6923 rads⁻¹

Power required to be supplied to the 2 motor,

P = τ ∗ ω

= 0.7495 W

Power required to be supplied to one motor,

P =

0.7495 W
2
= 0.3745 W

## 3 Ccomparison

- Required torque from the motor = 14.3736 oz − in
- Required RPM from the motor = 35.2589 rpm

These values correspond to the ideal world. But in practice, many losses are applied. Therefore, assuming that the losses are 50% or greater than the ideal values, we should at least double our requirements. Then,

Required torque from one motor, 14.3736 ∗ 2 = 28.7472 oz − in

Now, we need to consider the provided motor specifications to check whether or not the motor is suitable for our work. Consider the Toque vs. Speed and Torque vs. Current graph for Pololu Metal Gear motor 25Dx67L mm HP 12V with 48 CPR Encoder. According to the graph, for the 28.7472 oz-in torque (nearly30 oz-in), we can get nearly 215 RPM by this motor. It would give the robot plenty of speed. Furthermore, we can see that to achieve this we have to give nearly 1600 mA to the motor. So, we can reduce the voltage and decrease RPM of the motor to desired values. In our calculations, we didn’t consider the frictional and other losses. So, considering those conditions, this motor (Pololu 25D*67L mm HP) is a good fit and we chose it for our work.

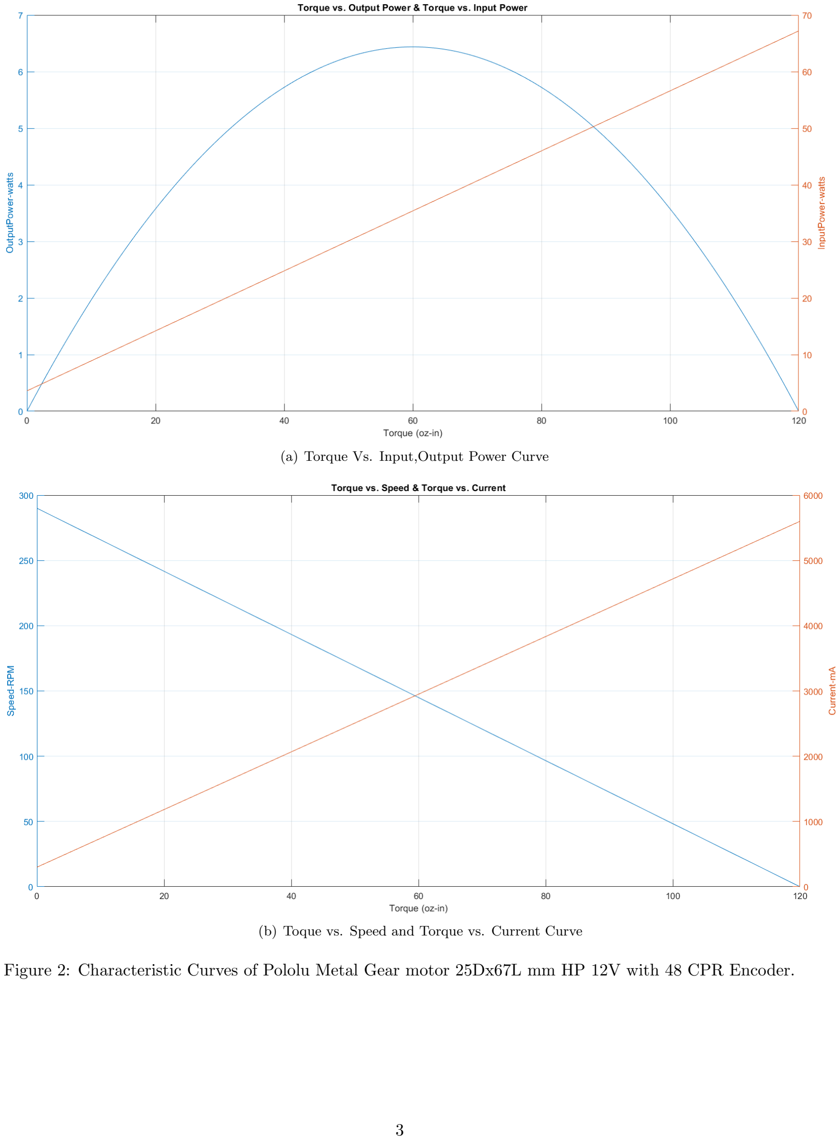
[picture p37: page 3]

(a) Torque Vs. Input,Output Power Curve
(b) Toque vs. Speed and Torque vs. Current Curve

Figure 2: Characteristic Curves of Pololu Metal Gear motor 25Dx67L mm HP 12V with 48 CPR Encoder.

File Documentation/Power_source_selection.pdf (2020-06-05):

# Power Source Selection

Group : BRAND | 180631J . 180564F . 180241M . 180411K . 180337M
| Submitted on June 5, 2020

## 1 Calculations

Note : Calculations were done assuming the worst case scenario where all the components are working at the same time drawing the respective maximum currents.

According to the calculations done in the Motor Selection stage (in order to choose the motor ) we observed that a torque of 28.7472 oz − in per one motor is more than enough to drive our mobile robot without any problem and corresponding required current will be lying in the range of 1000 mA -2000 mA. Therefore the maximum current that may be drawn by the motor can be approximated to be 2000 mA which is the critical factor when choosing a battery. For other motors their stall currents are used while for the sensors and drivers their normal currents are used.


Figure 1: Torque vs. Speed and Torque vs. Current curves for Pololu Metal Gear motor 25Dx67L mm HP 12V with 48 CPR Encoder.

Component | Operating Voltage | Max Current | Quantity | Total Current
| (V) | (mA) | | (mA)
Gear Motor | 12 | 2000 | 2 | 4000
MG996R servo Motor | 5 | 1400 | 2 | 2800
Arduino Mega2560(Rev3) | 5 | 800 | 1 | 800
MG90S servo Motor | 5 | 700 | 1 | 700
TCRT5000 IR Sensor | 5 | 60 | 8 | 480
HC-SR04 Ultrasonic Sensor | 5 | 15 | 3 | 45
L298N Motor Driver | 5 | 36 | 1 | 36
MPU-6050 Gyroscope | 3.3 | 4 | 1 | 4
TCS34725 Color Sensor | 3.3 | 0.152 | 1 | 0.152
Total Current Consumption | | | | 8865.152

Table 1: Current Consumption of Components

Maximum current related to the Arduino Mega2560(Rev3) board was decided depending on the maximum allowable current (which is 800 mA) of its LD1117S50CTR Voltage Regulator IC.

For the convenience of further calculations let’s assume that total current consumption is 9000 mA and we need to operate the robot with this current rate for half an hour.

Therefore the required capacity,

Reqired Capacity = 9000 mA ∗ 0.5h

= 4500 mAh

Since the battery should not be discharged more than 80% of its capacity due to safety issues the last 20% of its capacity must not be used and therefore the actual capacity a battery should have,

Actual required Capacity = 4500 mAh ∗ 120%

= 5400 mAh

Required minimum discharging rate (C value)

Dischaging rate =

9000 mA
5400 mAh
= 1.6667

Although the nominal voltage of the gear motor is 12V it is able to operate in any voltage in the range of 6V - 12V. Therefore we hope to provide about 9V to the motors . Therefore a Li-Po battery with 3 cells i.e 11.1V will be an ideal solution because we can provide that 9V requirement continuously by using proper voltage regulator.

Reqired V oltage = 11.1V

According to the above calculations we need to choose a battery with 11.1 voltage which has a capacity in the range of 5400 mAh with a discharging rate greater than 1.666C.

## 2 Battery Selection

Considering above requirement we selected XK Detect X380 11.1V 3S 5400mAh Lipo battery. This battery is designed with 3 cells placed in series.


Figure 2: Selected battery

### 2.1 Advantages and Specifications of our selection

We can identify several advantages including High energy density, high discharge rate, and no memory effect. Due to the small size, flat cell design, and the lightweight reduce the weight of our robot and ease the handling of the robot. There is no need for maintenance and have a long cycle life. Not like other batteries, this is pollution-free. Though this is expensive than other batteries, this is reliable and has high quality. With short circuit production function, it increases the safety.

Battery type | Lithium Polymer (Lipo Battery)
C rate | 20C
Cell configuration | 3S2P
Continuous Discharge | 20C (108A)
Max burst rate | 40C (216A)
Max volts per pack | 12.6V
Min volts per pack | 9V
Charge rate | 1C (5.4A)
Dimensions | 102mm*34mm*42mm
Weight | 0.309 kg

Table 2: Specification of selected battery

### 2.2 Comparison

There are two main types of batteries, rechargeable, and non-rechargeable. As non-rechargeable batteries can use only once and have to replace we consider rechargeable batteries. We can identify Lead-acid, NiCd, NiMH, Li-ion, and Lithium-ion polymer as rechargeable batteries most commonly used.

| NiCd | NiMH | Lead-acid | Li-ion | Li-ion polymer
Cell voltage (V) | 1.25 | 1.2 | 2 | 3.6 | 3.7
Overcharge tolerance | Moderate | Low | High | Very low | Low
Maintenance requirement | 30-60 days | 60-90 days | 3-9 months | Not required | Not required
Cost per cycle (US $) | 0.04 | 0.12 | 0.10 | 0.14 | 0.29
Fast charge time | 1h | 2-4h | 8-16h | 2-4h | 2-3h
Energy density (Wh/kg) | 45-80 | 60-120 | 30-50 | 110-160 | 100-130
Operating temperature (C) | -40 t0 60 | -20 to 60 | -20 to 60 | -20 to 60 | 0 to 60

## 3 Drawbacks of other batteries

### 3.1 Nickel Cadmium (Ni-Cd)

- elative low energy density
- Memory effect
- Environmentally unfriendly (contains toxic metals)
- High self-discharge rate

### 3.2 Nickel Metal Hydride (NiMH)

- High self-discharge rate
- Memory effect
- Need to store in cool place as performance degrades with elevated temperatures
- High maintenance
- Have less life cycle
- Limited discharge current
- Generate more heat during charge

### 3.3 Lead Acid

- Low energy density
- Environmentally unfriendly
- Transportation restrictions
- Thermal runaway with improper charging

### 3.4 Lithium Ion

- Require protection circuit
- Aging even if not in use
- Heavier
- More explosive

### 3.5 Lithium Polymer

- Expensive
- Lower energy density
- Can be dangerous if handled incorrectly

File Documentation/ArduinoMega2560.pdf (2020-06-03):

## Functionality of Arduino MEGA2560 (REV3) Peripheral Circuitry

Thalagala B.P. 180631J

April 29, 2020

The Arduino MEGA2560 is a microcontroller board based on the ATmega2560. It has 54 digital input/output pins (of which 15 can be used as PWM outputs), 16 analog inputs, 4 UARTs (hardware serial ports), a 16 MHz crystal oscillator, a USB connection, a power jack, an ICSP header, and a reset button[1].


Figure 1: Top view of the Arduino MEGA 2560 REV3 board[1]

## 1 Power Regulator Circuit

Power regular circuit is used to regulate the input voltage of the board form a voltage in range of 7V-12V to lower +5V, as this is the operating voltage of the Arduino MEGA board.It consists of following electronic components.


Figure 2: Power regulator schematic diagram[1]

### 1.1 Barrel connector

This barrel type connector is used to supply DC power (6V-12V is recommended) to the board from an external power source.

### 1.2 Reverse Voltage Protection Diode

If the polarity of input supply voltage is accidentally reversed the board may get damaged. This M7 diode (SMD version of 1N4007 diode) provides the protection at such situations.

### 1.3 Electrolytic Capacitors

Polarized capacitors are used to reduce possible small fluctuations(electrical noise) in the input voltage/current. Capacitors with fairly high capacitance (47µF) is used for this purpose as they can store high electric charge.

### 1.4 Non-polarized Capacitors

Although electrolytic capacitors have high capacitance it is considerably slow in discharging process due to its high series resistance (capacitive reactance). As a solution for this draw back,electrolytic capacitor is discharged through a non-polar capacitor with very low capacitance(100nF) and an extremely small discharging time.

### 1.5 LD1117S50CTR Voltage Regulator IC

This IC continues to work although the input voltage is very close to the required output, and able to handle currents up to 800 mA. Also it can regulate voltages in the range 6.5V to 15V to lower 5V level[3].

## 2 Clock Circuit

Micro-controllers use clock signal to trigger events and keep track of time as everything happens with respect to time. clock Circuitry is responsible of generating this clock signal which is basically an electronic signal periodically toggle between two states like a Square wave[5].


Figure 3: External oscillator schematic diagram[1]

1

### 2.1 Crystal Oscillator

Arduino MEGA 2560 uses 16 MHz oscillator to generate this clock signal. It consists of a piezoelectric Crystal resonator [4] and two ceramic capacitors in order to adjust resonance frequency.

3 | In-system | Programming/
In-circuit | Serial | Programming

## Circuit

Arduino MEGA2560 board has two ICSP headers named as ICSP1 and ICSP. Both headers have 6 pins and are arranged in 2 * 3 arrays. 6 pins are named as MISO, MOSI, SCK, V+(+5V), Ground, and Reset[2].


Figure 4: ICSP headers in an Arduino MEGA2560 board[1]

### 3.1 ATMEGA16U2 microcontroller

Programs related to USB to serial conversion are stored here. This supports to upload the programs into main ATMEGA2560 microcontroller, simply through the USB cable.

### 3.2 ICSP1

ICSP1 header is used to implement the USB to serial converter micro-controller(ATMEGA16U2 ).

### 3.3 ICSP

ICSP header is used to directly program the main microcontroller of the Arduino MEGA2560 board, whenever the USB to serial converter can not be used to program the microcontroller due to any failure of converter. To do this additional ISP/ICSP programmer(an electronic circuitry) is needed.

## 4 Reset Circuit

There are two mechanisms to reset the Arduino MEGA2560 board. One of them is manual while the other one is done by the USB to serial converter chip. Here the reset pin is active low, i.e. microcontroller get reset whenever the pin receives a low state signal.

### 4.1 Manual Method

To reset the microcontroller there is a TS42 type press button switch on the board. When it is pressed, reset pin is grounded. This process resets the microcontroller.


Figure 5: Manual resetting[1]

### 4.2 Reset through the ATMEGA16U2

In this method microcontroller get reset whenever a connection is made with the Arduino IDE through its USB cable. The required DTR(Data Terminal Ready)signal is sent by the ATMEGA16U2 to the RESET pin of the ATMEGA2560 at the beginning of each connecting.


Figure 6: Automatic resetting[1]

## Bibliography

[1] Arduino Mega 2560 Rev3 | Arduino Official Store. https://store.
arduino.cc/usa/mega-2560-r3. (https://store.arduino.cc/usa/mega-2560-r3)
[2] arduino | uno | - | ICSP | pin, | what | is | it | actually?
https://arduino.stackexchange.com/questions/40098/icsp-pin-what-is-it-actually. (https://arduino.stackexchange.com/questions/40098/icsp-pin-what-is-it-actually)
[3] LD1117xx | Datasheet | - | STMicroelectronics | | | DigiKey.
https://www.digikey.com/en/datasheets/stmicroelectronics/stmicroelectronics-en-cd00000544#pfd. (https://www.digikey.com/en/datasheets/stmicroelectronics/stmicroelectronics-en-cd00000544#pfd)
[4] Crystal | Oscillator | : | Working | and | Its | Various
Applications. | https://www.watelectronics.com/
crystal-oscillator-circuit-working-applications/, (https://www.watelectronics.com/crystal-oscillator-circuit-working-applications/) | September
2019.
[5] Wikipedia contributors. Electronic oscillator — Wikipedia, the free encyclopedia. https://en.wikipedia.org/w/index.php?title=Electronic_oscillator&oldid=953594751, (https://en.wikipedia.org/w/index.php?title=Electronic_oscillator&oldid=953594751) 2020. [Online; accessed 28-April-2020 ].

2

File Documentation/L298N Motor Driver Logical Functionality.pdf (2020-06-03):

## Functionality of DUAL FULL -BRIDGE DRIVER

Thalagala B.P. 180631J

May 4, 2020


Figure 1: Block Diagram of L298 DUAL FULL -BRIDGE DRIVER

In1 | In2 | EnA | Out1 | Out2
0 0 1 1 | 0 1 0 1 | 1 1 1 1 | 0 0 1 1 | 0 1 0 1
0 0 1 1 | 0 1 0 1 | 0 0 0 0 | 0 0 0 0 | 0 0 0 0

Figure 2: Truth table for Out1 and Out2 as functions of In1, In2 and EnA

1

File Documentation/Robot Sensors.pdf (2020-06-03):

Department of Electronic and Telecommunication Engineering

## University of Moratuwa, Sri Lanka

EN2532 - Robot Design and Competition


# ROBOT SENSORS

Submitted by

Thalagala B.P.

Sandeepa H.K.C.A

Hewavitharana D.R.

Nagasinghe K.R.Y.

Kumarasinghe H.A.N.H

180631J

180564F

180241M

180411K

180337M

Submitted on

## April 23, 2020

## TCRT5000 IR Sensor


Figure 1: TCRT5000 IR Sensor[3]

This sensor can be categorized as a reflective sensors. It has both a Photo-diode and a Photo-transistor coupled in its package. Photo-diode is used as a emitter which emits IR beam which has around 950 nm wave length. This IR beam is reflected if it meets a reflective object. The reflected IR beam is then detected by Photo-transistor of TCRT5000 sensor. So this sensor is mostly used for detect presence of the object or any other reflective surface in front it. There are so many sensors which do the same purpose. They are,

1 LED and LDR : LED is used as a sender and LDR is used as a receiver. This combination is also good because it is more reluctant to sunlight noise. But the receiver output is not enough to detect perfectly for colors which has less difference from white. And also it must be calibrated frequently.

2 LASER DIODE and LDR : Sender is a Laser diode and LDR is the receiver. In every way this combination perform very well. There are no issue from sunlight and also environment because laser beam has very high density. If the surrounding has same color which emits from the laser , there will be an error. And the laser diodes are expensive , so if we create sensor panels we have to spend considerable amount of money.

3 White color LED with high intensity and LDR : When we use this combination there will be no issue from surrounding colors as other sensor combinations. Here also LDR is used as a receiver. High intensity of LED prevents effects from sunlight. But for the optimum result we have to keep very low distance between the sensor and surface.

4 IR LED and Photo-transistor (TCRT 5000) : It was mention previously as topic. There is a issue also. It can recognize only white and black with complete accuracy.

Considering all of these sensors and our task we can easily select IR sensors (TCRT 5000). Its color sensing error does not valid for our task because it has only white lines on black background. TCRT 5000 sensor is covered and it blocks unwanted light which comes from the environment. And also the emitter and receiver are separate by each other to prevent unwanted reflections. So this one is more truthful and efficient than other. And it has a low cost. So it is better instead of (1) and (2) (mentioned above). Considering (3) it needs low distance. But our task has ramp area and we need required speed. So considering our task this combination (3) is not suitable for us.
In our project this sensor ( TCRT 5000 ) is used for detecting white line which is on the black background. White surface is known as reflective surface and black is not. So we can detect the presence of white lines. Our sensor panel configuration consists 8 IR sensors and each one has a special position. According to this placements robot brain can verify where the robot is. It has several specifications such as[3],

IR sensor with transistor output
Operating Voltage | 3V - 5V
Diode forward Current | 60mA
Output | Analog or digital
Transistor collector current | 100mA (maximum)
Operating temperature | -25◦C to +85◦C
Operating range | 0.2mm – 15mm
Dimensions[4] (L ∗ W ∗ H in mm) 10.2 x 5.8 x 7

Table 1: TCRT 5000 IR Sensor features and specs

When sensor is powered and began to sense, there will be an analog output which can also be vary according to environmental conditions (mainly day light ). Therefore it is not possible to guarantee 100% accurate analog to digital conversion as we expect. So a comparator circuit which consists of LM324 operational amplifiers is used in addition to the normal sensors to take clear digital output.

## HC-SR04 Ultrasonic Sensor

This is a proximity sensor, also known as an ultrasonic transducer based on a transmitter and a receiver and mainly used to determine the distance to a target object. In our case, we use this sensor to detect distances to the colored box and to the walls in wall following part. So, we have to use three ultrasonic sensors to achieve this task. Two sensors are attached on the left and right sides of the robot to detect the distance to the wall. One sensor is attached in front of the robot to detect the distance to the box.


Figure 2: HC-SR04 Ultrasonic Sensor and Its Object detecting Method

It comes as a complete package with an ultrasonic transmitter and a receiver. The amount of time it takes to send and receive waves will determine how far the object is placed from the sensor. It mainly depends on the sound waves working on “non-contact” technology. The required distance of the target object is measured without any damage, giving accurate and precise details. Here’s a list of some of the HC-SR04 ultrasonic sensor features and specs[6].

Power Supply | +5V DC
Quiescent Current | Less than 2mA
Working Current | 15mA
Effectual Angle | Less than 15◦
Ranging Distance | 2cm – 400 cm/1” – 13ft
Resolution | 0.3 cm
Measuring Angle | 30 degree
Trigger Input Pulse width | 10uS
Dimension | 45mm x20mm x15mm

Table 2: HC-SR04 ultrasonic sensor features and specs

Our need to use this sensor is to measure distances to obstacles. There are several different sensors that can perform this function as Infra-Red (IR) range sensor, Ultrasonic Sensor, Laser Range Sensor. But, apart from the Ultrasonic sensor, there are some drawbacks when using other sensors. There are a lot of limitations in infrared sensors, like the inability to use them in sunlight due to interference[5]. Therefore, our measurements may change due to the light conditions in the environment.
Ultrasonic sensors work using sound waves, therefore detecting obstacles is not affected by many factors such as Light, Dust, Smoke, Mist, Vapor and Lint. So, the Ultrasonic sensor is more reliable than using the

IR sensor. The Laser Range Sensor is better than these two sensors because it has higher accuracy and resolution than the others. But we don’t need that much precision or resolution for our task. Also, Laser Range Sensor is a high cost devise. So, the Ultrasonic Sensor is more effective than the others in achieving our purpose.

## TCS34725 - Color Sensor

A Color Sensor is a device which detects or senses colors. A color sensor uses an external means of emitting light (like an array of white LEDs) and then analyses the reflected light from the object in order to determine its specific color.
There are many color sensors available. Some of them are TCS230, TCS3200 and TCS34725 etc. The TCS230, TCS3200 and TCS3210 senses color light, with the help of an 8 x 8 array of photo-diodes[9] and use a Current-to-Frequency Converter on the readings of it to convert them into a square wave with a frequency directly proportional to the light intensity which is less accurate than the sensor TCS34725 that we use.


Figure 3: TCS34725 - Color Sensor

An IR blocking filter, integrated on-chip and localized to the color sensing photodiodes, minimizes the IR spectral component of the incoming light and allows color measurements to be made accurately. The sensor additionally has an amazing 3,800,000:1 unique range with flexible incorporation time and increase so it is appropriate to use behind obscured glass. The high sensitivity, wide dynamic range, and IR blocking filter make the TCS34725 an ideal color sensor solution to use under varying lighting conditions and through attenuating materials. In addition, the IR blocking filter enables the TCS34725 to perform

Ambient Light Sensing (ALS). The TCS34725, itself, can enter a lower-power wait state between light sensing measurements to further reduce the average power consumption[10].

## MPU-6050 Gyroscope


Figure 4: MPU-6050 Gyroscope[2] with its Pinout[8]

This sensor is used to identify the angle of the robot and giving a feedback so that the motor speed of the robot could be changed likewise. This is very useful in the ramp activity, so that the speed of the robot can be controlled. The MPU-6050 consists of a 3-axis gyroscope and a 3-axis accelerometer on the same silicon die, together with an onboard Digital Motion Processor capable of processing complex 6-axis motion fusion algorithms. The device can access external magnetometers or other sensors through an auxiliary master I2C bus. If 3-axis Magnetometer is connected to auxiliary I2C bus, then MPU6050 can provide complete 9-axis Motion Fusion output. This has a built-in voltage regulator[7].
There are some other types of gyroscope sensors too that can be used for this purpose such as,

1 ADXL335

2 ADXL345

3 MMA7361

4 LIS3DH Triple-axis accelerometer module

All above modules are 3-axis gyroscopes and 3-axis accelerometers. ADXL 335, ADXL345 are low power consumption sensor modules. The modules generate separate analog voltage for each axis. MMA7361 has a sleep mode and a select pin which can be helpful to save power. Above three modules have low power consumption and easy to use and program but do not have onboard digital motion processors (DMP) unlike MPU-6050. So, as we need an onboard DMP for control of the robot above three modules are not much of a use. The LIS3DH module is an intelligent, low-power, capacitive, micro-machined accelerometer with 12-bit resolution. But this module also doesn’t have a digital motion processor like MPU-6050. So MPU-6050 is the most suitable gyroscope sensor for the project[1].

## Bibliography

[1] MPU-6050 | TDK. https://invensense.
tdk.com/products/motion-tracking/6-axis/ mpu-6050/. (https://invensense.tdk.com/products/motion-tracking/6-axis/mpu-6050/)
[2] MPU6050 | (Gyroscope | Accelerometer
Temperature) Sensor Module |.. | https://
www.electronicwings.com/sensors-modules/ mpu6050-gyroscope-accelerometer-temperature-sensor-module. (https://www.electronicwings.com/sensors-modules/mpu6050-gyroscope-accelerometer-temperature-sensor-module)
[3] TCRT5000 | IR | Sensor | Pinout,
Equivalent, | Circuit | & | Datasheet.
https://components101.com/sensors/tcrt5000-ir-sensor-pinout-datasheet. (https://components101.com/sensors/tcrt5000-ir-sensor-pinout-datasheet)
[4] TCRT5000, | TCRT5000L | Reflective | Optical
Sensor | With | Transistor | Output | | Vishay.
http://www.vishay.com/optical-sensors/list/product-83760/. (http://www.vishay.com/optical-sensors/list/product-83760/)
[5] Ultrasonic vs Infrared (IR) Sensors - Which is better? https://www.maxbotix.com/articles/ultrasonic-or-infrared-sensors.htm, (https://www.maxbotix.com/articles/ultrasonic-or-infrared-sensors.htm) November 2017.
[6] Complete | Guide | for | Ultrasonic
Sensor | HC-SR04 | with | Arduino.
https://randomnerdtutorials.com/complete-guide-for-ultrasonic-sensor-hc-sr04/, (https://randomnerdtutorials.com/complete-guide-for-ultrasonic-sensor-hc-sr04/) July 2018.
[7] Gyroscope | Sensor- | Working, | Types | &
Applications. | https://www.elprocus.com/
gyroscope-sensor/, (https://www.elprocus.com/gyroscope-sensor/) August 2019.
[8] MPU6050 | pinout- | wiring | diagram | and
sample | projects. | https://pinouts.net/
mpu6050-pinouts-and-wiring-diagrams/, (https://pinouts.net/mpu6050-pinouts-and-wiring-diagrams/) October 2019.
[9] Dejan. | Arduino Color Sensing Tutorial -
TCS230 TCS3200 Color Sensor. | https://
howtomechatronics.com/tutorials/arduino/ arduino-color-sensing-tutorial-tcs230-tcs3200-color-sensor/, (https://howtomechatronics.com/tutorials/arduino/arduino-color-sensing-tutorial-tcs230-tcs3200-color-sensor/) May 2016.
[10] Adafruit Industries. RGB Color Sensor with IR
filter and White LED - TCS34725. https://www.adafruit.com/product/1334.

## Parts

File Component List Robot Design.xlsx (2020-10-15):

Component | Price | Place | nos | Val | Name | Date | Amount
 |  |  |  |  | Nikeshi | 2020-09-24 | 5000
 |  |  |  |  | Avishka | 2020-09-25 | 3000
LM2596S 3-40V to 1.5-35V 4A DC to DC Adjustable Step-Down Buck Module | 150 | tronic.lk | 4 | 600 | Bimalka | 2020-09-25 | 1000
Arduino MEGA Original Development Board with USB Cable (DB0003) | 1950 | tronic.lk | 1 | 1950 | Nagasinghe | 2020-09-25 | 2000
Dagaya 2.0 – VNH5019 Based Dual Motor Driver | 2950 | Aptinex | 1 | 2950 | Bimalka | 2020-09-28 | 3000
Raykha S8 | 800 | Aptinex | 2 | 1600 | Darsha | 2020-09-28 | 5000
Jumpers | 140 | tronic.lk | 4 | 560 | Bimalka | 2020-09-30 | 800
Sharp IR sensors | 950 | tronic.lk | 2 | 1900 | Avishka | 2020-10-06 | 1015
Caster Wheel Steel Ball 25.4mm | 120 | tronic.lk | 1 | 120 | Nagasinghe | 2020-10-07 | 320
Laser cutting two platforms and parts of the robot arm | 1850 | Pro | 1 | 1850 | Bimalka | 2020-10-08 | 565
Battery, wheels, charger through Devinda | 7700 | unitek | 1 | 7700 | Bimalka | 2020-10-14 | 920
5A buck, fuses, male-femal jumbers | 715 | tronic.lk | 1 | 715 | Bimalka |  | 1100
Nuts and Bolts | 300 | tronic.lk | 1 | 300
Encoder Protection shield : v1 | 320 | CB3D | 1 | 320
Power Supply base Laser cut, | 300 | Lasercutting.lk | 1 | 300
spacers | 265 | Scion | 1 | 265
Gripper Base 3D Print | 1100 | CB3D | 1 | 1100
Arm base laser cut | 500 | Lasercutting.lk | 1 | 500
3mm Nuts and bolts | 420 | Anakade(pvt) Ltd | 1 | 420
 |  |  |  |  | Total Investment |  | 23720
cost |  |  |  | 23150

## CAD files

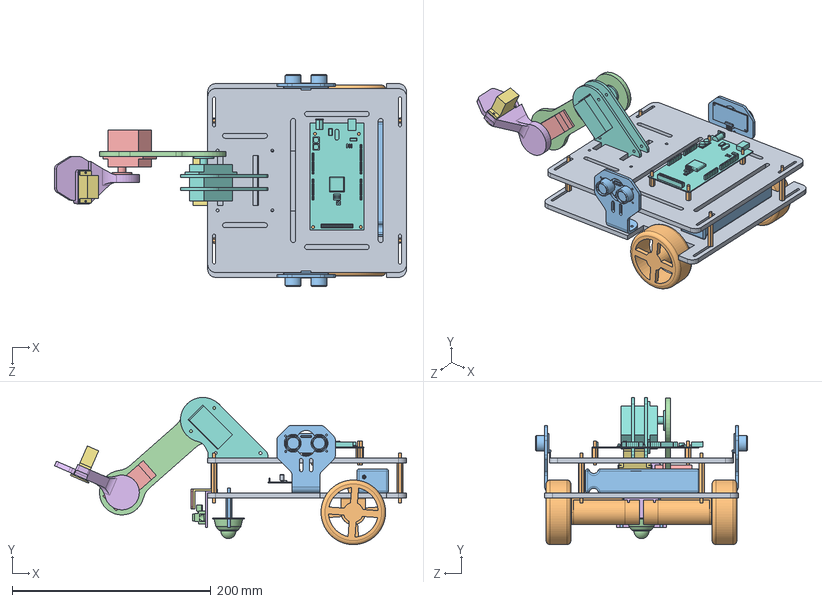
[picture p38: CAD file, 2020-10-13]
SolidWorksModels/ROBO BRAND.SLDASM
354.1 x 148.1 x 213.0 mm
PLATFORM
DriverWheel x 2
USsidesensor x 2
MAIN ARM PART1
MG996R SERVO
GRIPPER BASE
MG90 SERVO
NEWARM-BASE.WITH SERVO
PLATFORM2
SPACER x 4
CASTER SPACERS x 2
robotCasterWheel
COLORSENSOR
HOLDER COLOR AND US
COLORSEN HOLDER
Arduino Mega Board
Power Supply Unit
PCB SPACERS x 4
Battety
Long Range SHARP IR Sensors - #GP2Y0A21YK0F

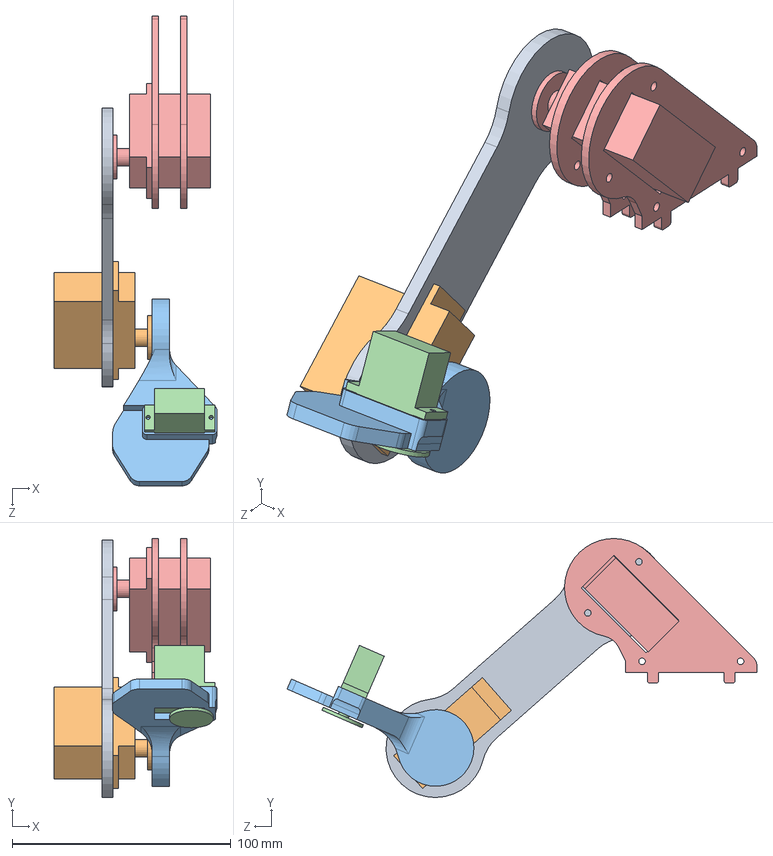
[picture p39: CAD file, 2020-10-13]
SolidWorksModels/Robot arm/ROBOT ARM SEMIFINAL REV1.SLDASM
74.3 x 118.3 x 214.6 mm
MAIN ARM PART1
MG996R SERVO
GRIPPER BASE
MG90 SERVO
NEWARM-BASE.WITH SERVO

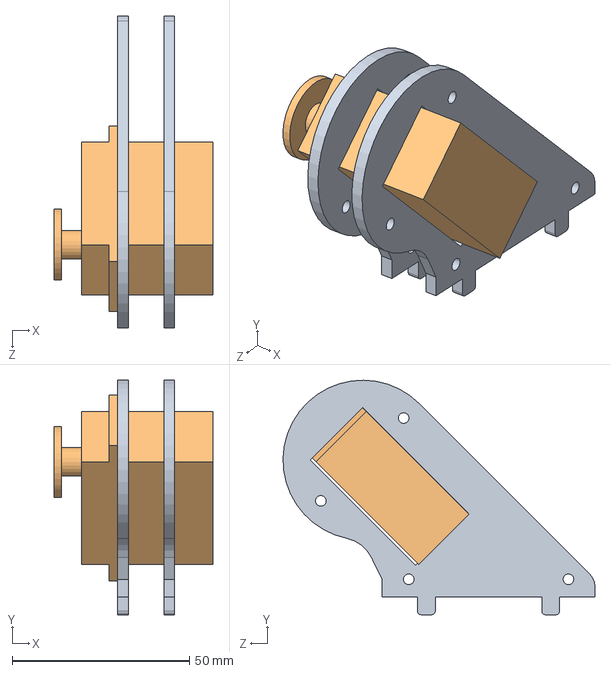
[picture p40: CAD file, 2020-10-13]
SolidWorksModels/Robot arm/NEWARM-BASE.SLDASM
44.7 x 66.1 x 87.9 mm
ARMBASE--NEW--DXF x 2
MG996R SERVO

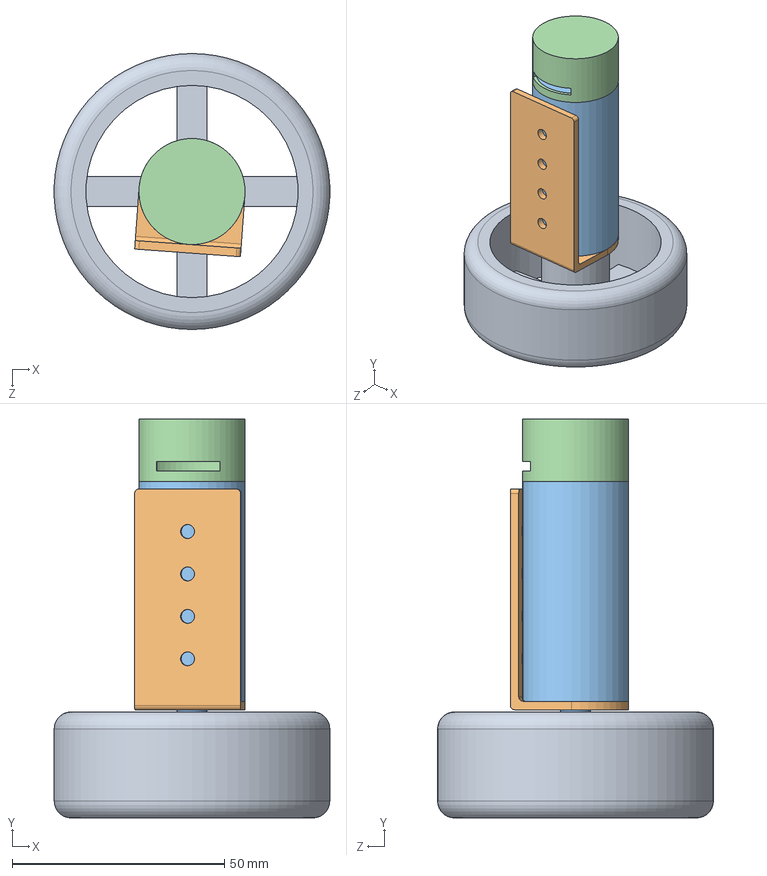
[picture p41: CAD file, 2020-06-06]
SolidWorksModels/Motors and Wheels/Motor&WheelsFinalAssembly.SLDASM
64.9 x 94.0 x 65.0 mm
robotWheels
RobotSocketMotor
robotMotor
RobotCap

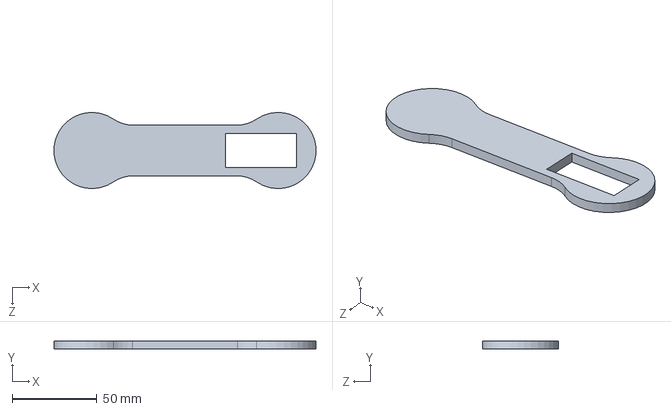
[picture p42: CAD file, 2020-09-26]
SolidWorksModels/Robot arm/MAIN ARM PART1.SLDPRT
154.8 x 5.00 x 45.0 mm

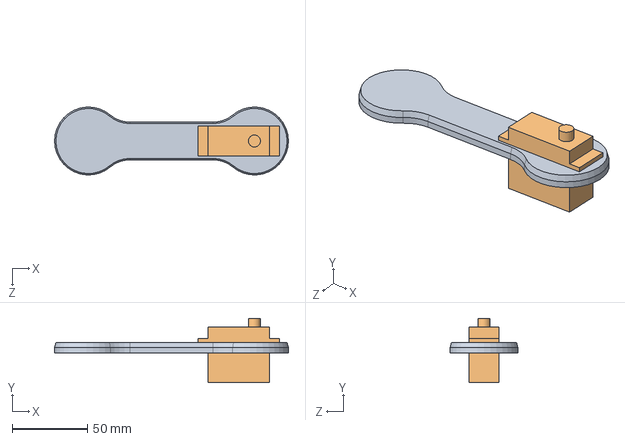
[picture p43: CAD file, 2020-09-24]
SolidWorksModels/Robot arm/ROBOT ARM MODEL REV1.SLDASM
155.0 x 42.7 x 44.9 mm
MAIN ARM PART1
MG996R SERVO

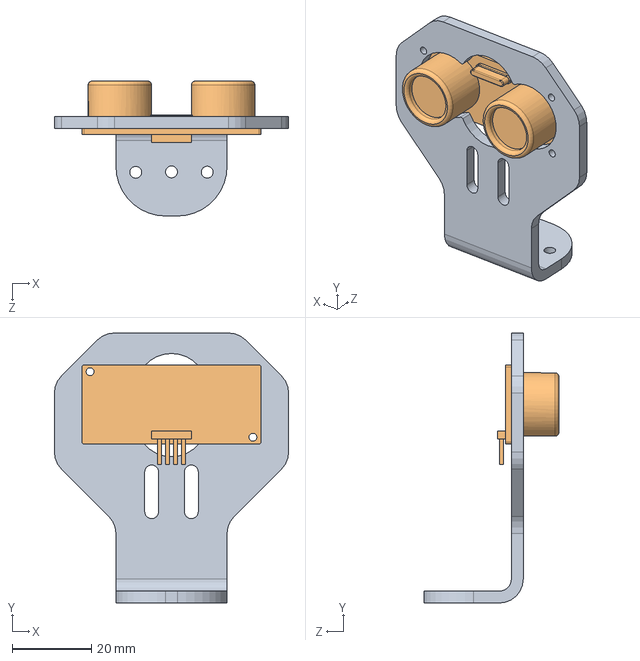
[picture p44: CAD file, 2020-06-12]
SolidWorksModels/Assem1.SLDASM
59.0 x 68.0 x 34.0 mm
Sensor holder
Ultrasonic Sensor

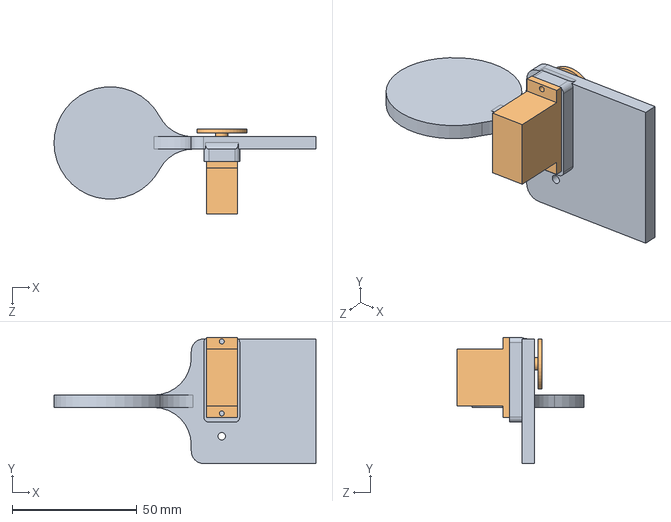
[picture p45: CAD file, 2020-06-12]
SolidWorksModels/Robot arm/Assem1.SLDASM
105.0 x 50.6 x 50.9 mm
GRIPPER BASE
MG90 SERVO

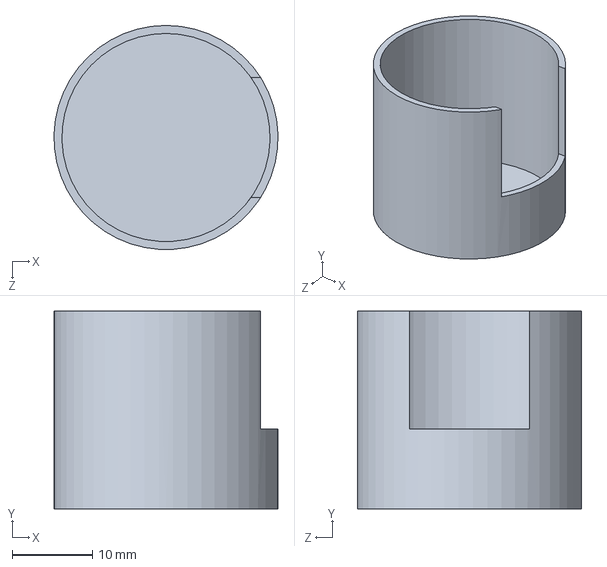
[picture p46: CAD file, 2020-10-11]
3D Print/RobotCap.SLDPRT
28.0 x 24.7 x 28.0 mm

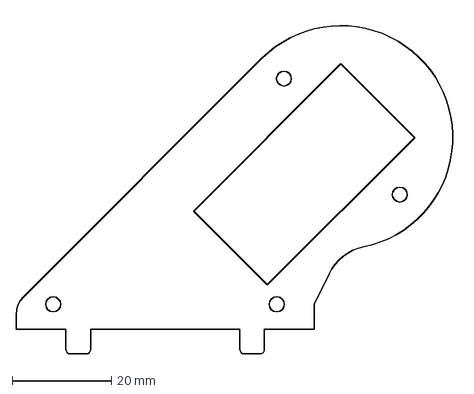
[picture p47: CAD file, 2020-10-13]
Laser Cut parts/ARMBASE--NEW.DXF
88.9 x 68.0 mm

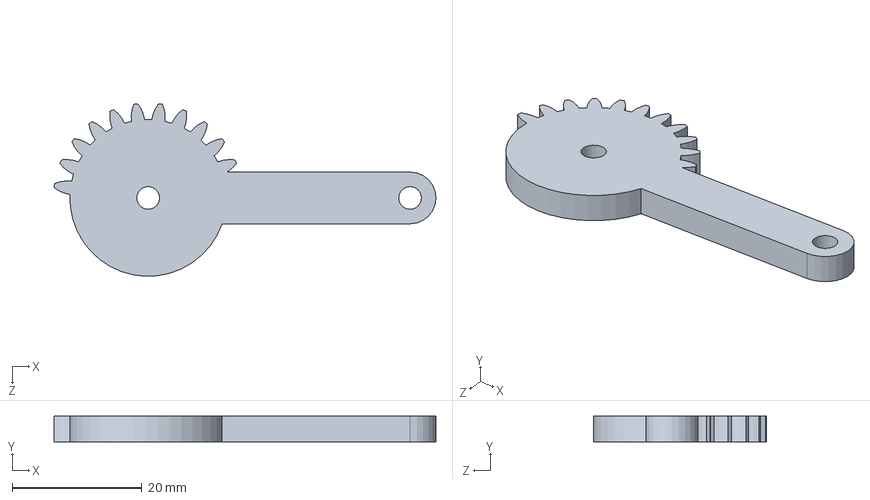
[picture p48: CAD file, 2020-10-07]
SolidWorksModels/GripperMechanismParts/DRIVEN-GEAR.SLDPRT
59.0 x 4.00 x 26.6 mm

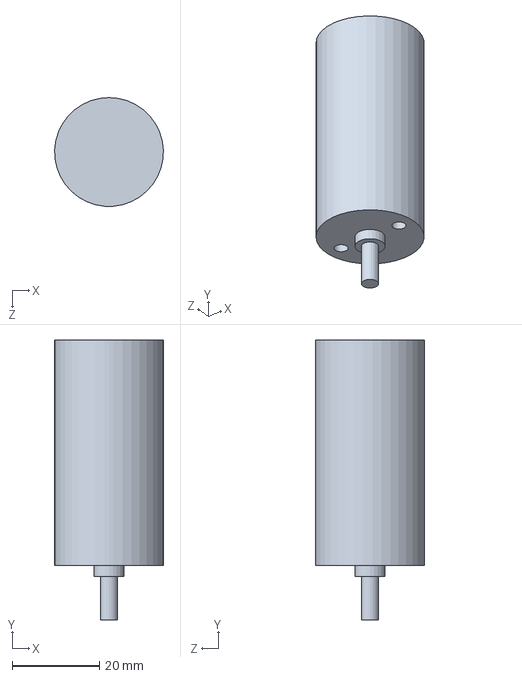
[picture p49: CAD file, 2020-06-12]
SolidWorksModels/Motors and Wheels/robotMotor.SLDPRT
25.0 x 64.3 x 25.0 mm

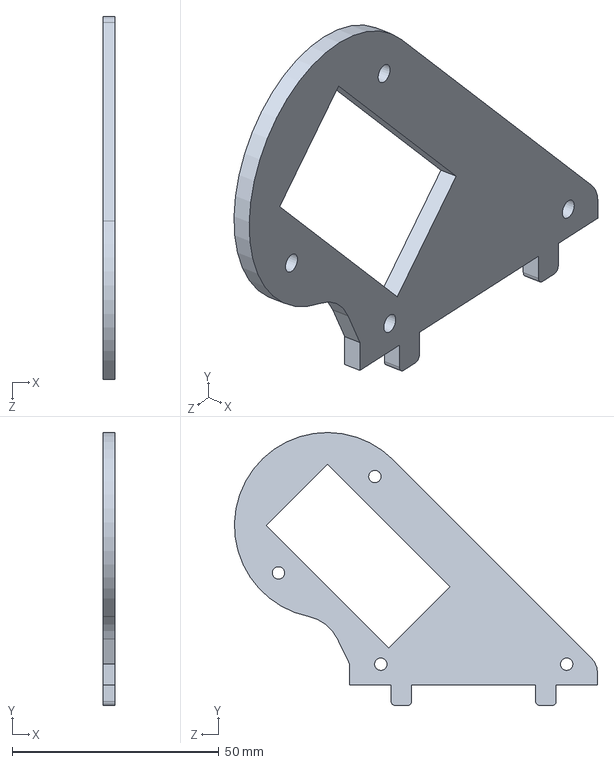
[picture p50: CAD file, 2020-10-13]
SolidWorksModels/Robot arm/ARMBASE--NEW--DXF.SLDPRT
3.00 x 66.1 x 87.9 mm

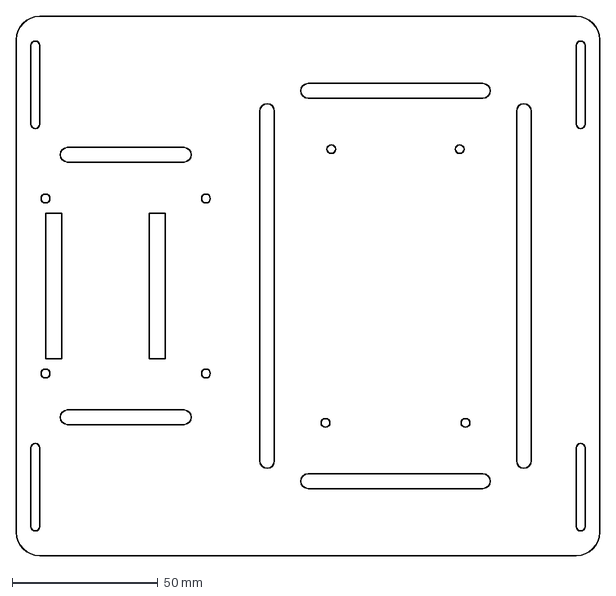
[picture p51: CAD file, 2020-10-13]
Laser Cut parts/PLATFORM-new.DXF
200.0 x 185.0 mm

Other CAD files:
SolidWorksModels/Robot arm/Assem3.SLDASM
3D Print/RobotCapNew.STL
SolidWorksModels/GripperMechanismParts/LINK.SLDPRT
SolidWorksModels/Motors and Wheels/RobotSocketMotor.SLDPRT
3D Print/ARM BASE.STL
3D Print/GRIPPER BASE.STL
3D Print/GRIPPER BASE2.STL
Laser Cut parts/ACT GEAR.DXF
Laser Cut parts/ARM.DXF
Laser Cut parts/BASE.DXF
Laser Cut parts/DRVN GEAR.DXF
Laser Cut parts/GRIPPER.DXF
Laser Cut parts/LINK.DXF
Laser Cut parts/PLATFORM.DXF
Laser Cut parts/Power Supply base.DXF
SolidWorksModels/Arduino Mega Board.SLDPRT
SolidWorksModels/Battery.SLDPRT
SolidWorksModels/Battety.SLDPRT
SolidWorksModels/COLORSEN HOLDER.SLDPRT
SolidWorksModels/COLORSENSOR.SLDPRT
SolidWorksModels/DriverWheel.SLDPRT
SolidWorksModels/GripperMechanismParts/ACTUATING-GEAR.SLDPRT
SolidWorksModels/GripperMechanismParts/GRIPPER.SLDPRT
SolidWorksModels/HOLDER COLOR AND US.SLDPRT
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

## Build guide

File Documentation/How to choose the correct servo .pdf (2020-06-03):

# Choose a proper Servo Motor

Thalagala B.P. 180631J

June 4, 2020

## 1 Usage of Servo Motors in the Mobile Robot

In our robot servo motors are used only to control the robot arm which we hope to use to lift the box which we need to inspect the color of the bottom side. To achieve this task we planned to use a robot arm consisting of three servo motors. Two of them are used to operate the arm and the gripper base while the remaining servo is used to control the gripper mechanism which holds the box.

### 1.1 Calculations for the required torques

Perpendicular distances to the lines of action of gravitational forces become maximum when the robot arm at the position depicted in the Figure 1. Therefore the maximum torque about the shafts of servo motors can be expected at this position. If a servo motor can overcome this maximum torque we can assume that it will definitely be able to handle any other torque it may come across during the operation.

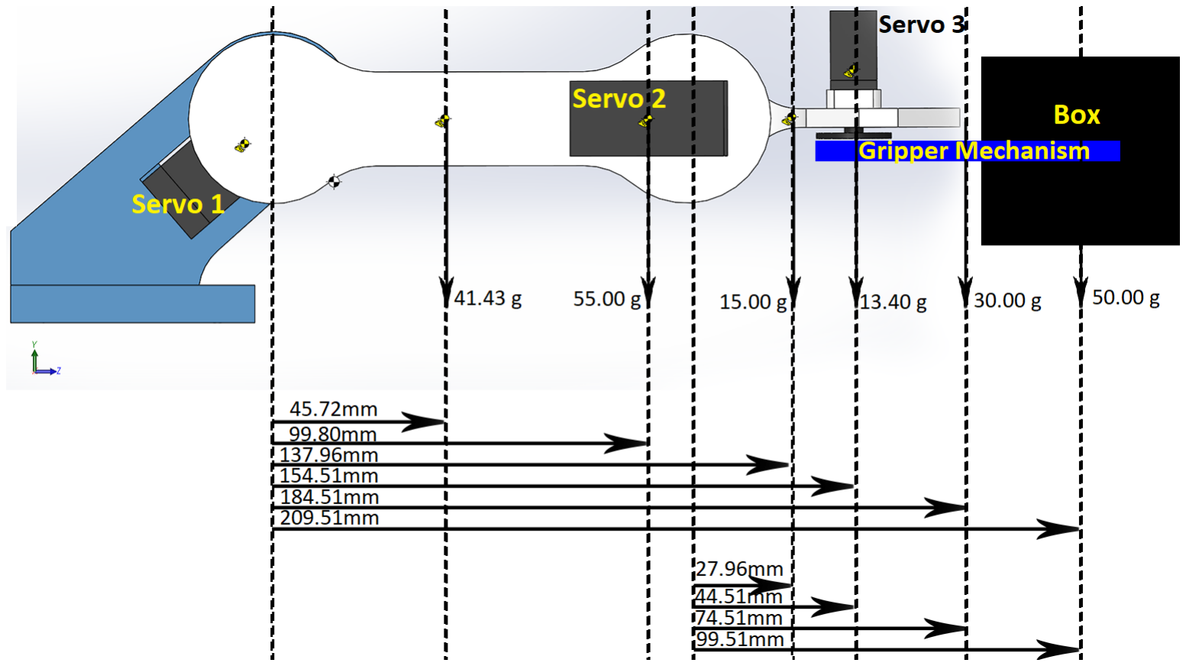
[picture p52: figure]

Figure 1: Free Force Diagram of the robot arm and approximated distances to the lines of action of gravitational forces

For the calculations, properties of one of the common 3D printing materials Acrylonitrile Butadiene Styrene (ABS) plastic is considered and mass of the following parts were taken through Mass Properties calculator in the SolidWorks Application and therefore 100% accuracy can not be guaranteed.

Mass of the gripper base | 15.00 grams
Mass of the arm | 41.43 grams

In addition to that mass of the gripper mechanism assumed to be 30.00 grams and mass of the box was taken as 50.00 grams which will possibly be less than that.

### 1.1.1 Torque about shaft of Servo 1

MAX(τ ) = 41.43 ∗ 45.72 + 55.00 ∗ 99.80 + 15.00 ∗ 137.96 + 13.40 ∗ 154.51 + 30.00 ∗ 184.51 + 50.00 ∗ 209.51 = 2.7534 ∗ 10⁴
g mm
= 2.7534 Kg cm

### 1.1.2 Torque about shaft of Servo 2

MAX(τ ) = 15.00 ∗ 27.96 + 13.40 ∗ 44.51 + 30.00 ∗ 74.51 + 50.00 ∗ 99.51 = 8.2266 ∗ 10³
g mm
= 0.82266 Kg cm

### 1.2 Selection of Servo Motors

Calculations were done assuming the ideal conditions and 100% efficiency can not be expected form motors in real world application and therefore servo motors are selected in a way that they can handle at least twice the above calculated torques easily.

For the Servo 1 and 2 TowerPro MG996R servo motor was chosen which has following characteristics

Weight | 55g
Dimension | 40.7*19.7*42.9 mm³
Stall torque | 9.4kg/cm (4.8v); 11kg/cm (6.0v)
Operating speed | 0.19sec/60degree (4.8v); 0.15sec/60degree (6.0v)
Operating voltage | 4.8- 6.6v
Gear Type | Metal gear
Dead band width | 1us

Table 1: Characteristics of TowerPro MG996R servo [2]

For the Servo 3 which is use to operate the gripper mechanism which is not mass critical, TowerPro MG90S micro servo motor was chosen which has following characteristics.

Weight | 13.4g
Dimension | 22.8*12.2*28.5mm
Stall torque | 1.8kg/cm (4.8V); 2.2kg/cm (6.6V)
Operating speed | 0.10sec/60degree (4.8V); 0.08sec/60degree (6.0V)
Operating voltage | 4.8V
Gear Type | Metal gear
Dead band width | 1us

Table 2: Characteristics of TowerPro MG90S servo [1]

### 1.3 Modified Initial Protype

Note : The gripper mechanism is not shown in the following models

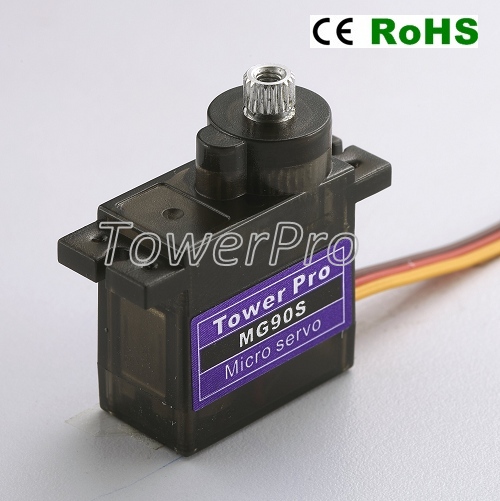
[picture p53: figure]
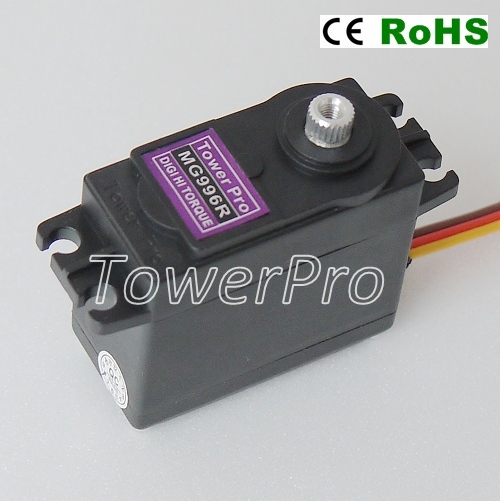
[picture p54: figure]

(a) TowerPro MG90S servo | (b) TowerPro MG996R servo

Figure 2: Selected servo

## Bibliography

[1] admin. MG90S | Tower Pro. http://www.towerpro.com.tw/product/mg90s-3/.
[2] admin. MG996R | Tower Pro. http://www.towerpro.com.tw/product/mg996r/.

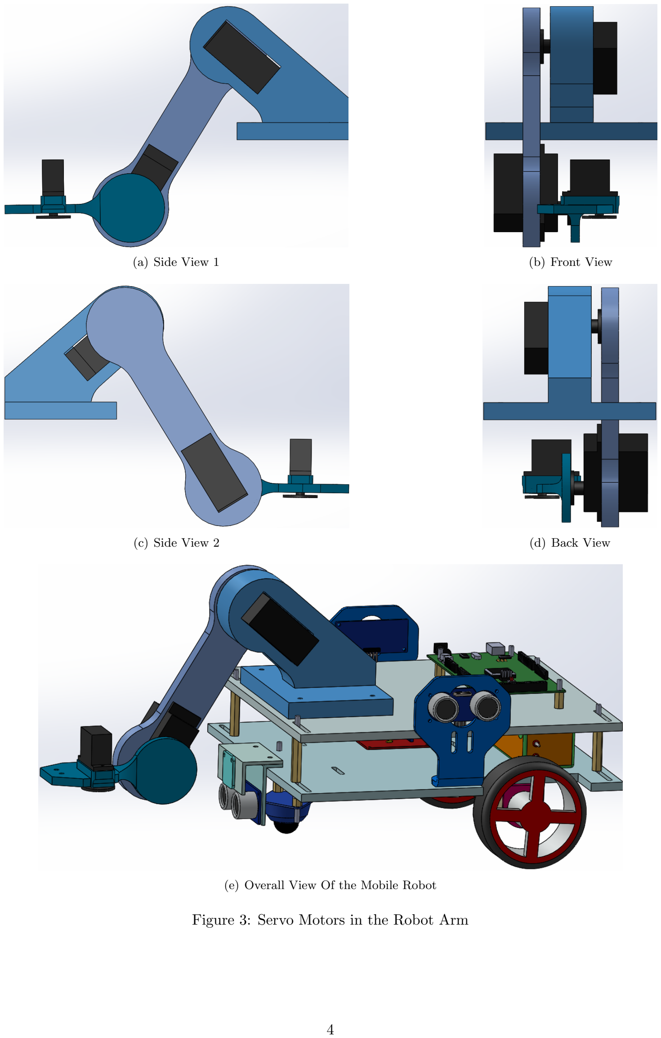
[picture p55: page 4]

(a) Side View 1 | (b) Front View
(c) Side View 2 | (d) Back View
(e) Overall View Of the Mobile Robot

Figure 3: Servo Motors in the Robot Arm

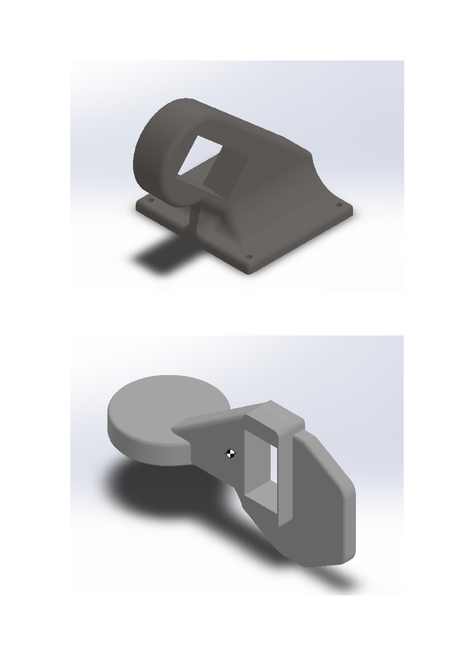
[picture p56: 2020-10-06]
3D Print/Untitled-1.jpg

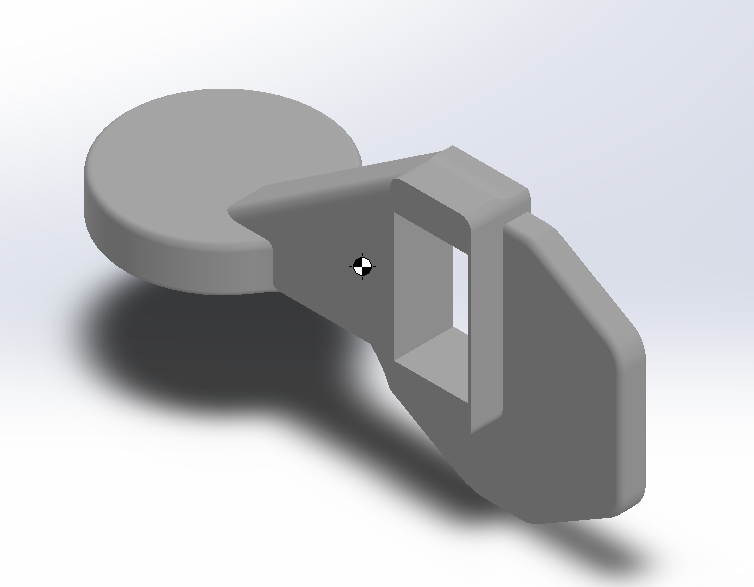
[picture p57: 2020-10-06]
3D Print/GRIPPER BASE.PNG

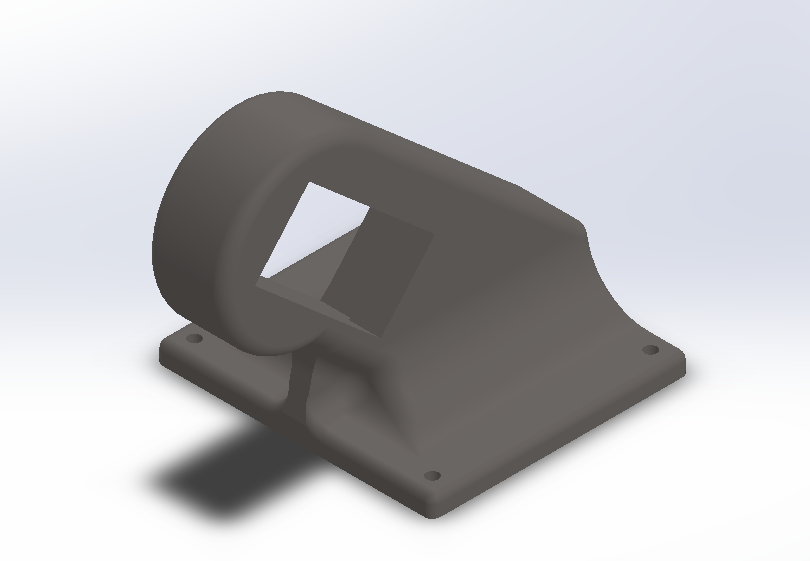
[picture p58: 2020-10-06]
3D Print/ARM BASE.PNG

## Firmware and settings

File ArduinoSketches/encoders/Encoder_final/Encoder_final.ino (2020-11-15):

//Author: Ravindu Nagasinghe
#include <DualVNH5019MotorShield.h>
// pins for the encoder inputs
#define RH_ENCODER_A 3 
#define RH_ENCODER_B 5
#define LH_ENCODER_A 2
#define LH_ENCODER_B 4
 
// variables to store the number of encoder pulses
// for each motor
volatile unsigned long leftCount = 0;
volatile unsigned long rightCount = 0;
int millimetersLeft = 180;// just defining length to travel for left encoder
int millimetersRight = 10;// just defining length to travel for Right encoder
int millimetersStraight = 50;// just defining length to travel for  encoder to go straight
DualVNH5019MotorShield motors;
void setup() {
  motors.init();
  pinMode(LH_ENCODER_A, INPUT);
  pinMode(LH_ENCODER_B, INPUT);
  pinMode(RH_ENCODER_A, INPUT);
  pinMode(RH_ENCODER_B, INPUT);
  
  // initialize hardware interrupts
  attachInterrupt(digitalPinToInterrupt(2), leftEncoderEvent, CHANGE);//2 is the LH Encoder A value
  attachInterrupt(digitalPinToInterrupt(3), rightEncoderEvent, CHANGE);//3 is the RH Encoder A value
  
  Serial.begin(9600);
  
}

void loop() {
int drivedistanceLeft(int millimetersLeft);// function to give the needed distance to travel for left encoder
int drivedistanceRight(int millimetersRight);// function to give the needed distance to travel for right encoder
int drivedistanceStraight(int millimetersStraight);// function to give the needed distance to travel straight for any encoder
}
void drivedistanceStraight(int millimetersStraight){
  motors.setSpeeds( 00,  00);
  delay(10);
  int tickGoalStraight = (35*millimetersStraight)/10;// Defining number of ticks required to travel the distance
  while ((leftCount<tickGoalStraight) || (rightCount<tickGoalStraight)){
    motors.setSpeeds( 20,  20);//starting motors to trael needed distance
    delay(1000);
    }
    motors.setSpeeds( 00,  00);//stopping motors after the required distance
    delay(10);
  }
void drivedistanceLeft(int millimetersLeft){
  motors.setSpeeds( 00,  00);
  delay(10);
  int tickGoalLeft = (35*millimetersLeft)/10;// Defining number of ticks required to travel the distance
  while (leftCount<tickGoalLeft){
    motors.setSpeeds( 20,  -20);//starting motors to trael needed distance
    delay(1000);
    }
    motors.setSpeeds( 00,  00);//stopping motors after the required distance
    delay(10);
  }
 void drivedistanceRight(int millimetersRight){
  motors.setSpeeds( 00,  00);
  delay(10);
  int tickGoalRight = (35*millimetersRight)/10;// Defining number of ticks required to travel the distance
  while (rightCount<tickGoalRight){
    motors.setSpeeds( -20,  20);//starting motors to trael needed distance
    delay(1000);
    }
    motors.setSpeeds( 00,  00);//stopping motors after the required distance
    delay(10);
 }

// encoder event for the interrupt call
void leftEncoderEvent() {
  if (digitalRead(LH_ENCODER_A) == HIGH) {
    if (digitalRead(LH_ENCODER_B) == LOW) {
      leftCount++;
    } else {
      leftCount--;
    }
  } else {
    if (digitalRead(LH_ENCODER_B) == LOW) {
      leftCount=0;
    } else {
      leftCount++;
    }
  }
}
 
// encoder event for the interrupt call
void rightEncoderEvent() {
  if (digitalRead(RH_ENCODER_A) == HIGH) {
    if (digitalRead(RH_ENCODER_B) == LOW) {
      rightCount++;
    } else {
      rightCount--;
    }
  } else {
    if (digitalRead(RH_ENCODER_B) == LOW) {
      rightCount=0;
    } else {
      rightCount++;
    }
  }
}

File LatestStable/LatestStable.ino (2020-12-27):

//Last Modified : 

//************************Including necessary libraries*************************
#include <DualVNH5019MotorShield.h> // Library for motor driver
#include <SharpIR.h> // Library for SharpIRs
#include <Wire.h> // Library for I2C communication
#include <Adafruit_PWMServoDriver.h> // Library for servo driver

// *******************************Defining macros*******************************
#define SERVO_FREQ 50 // Analog servos run at ~50 Hz updates
#define Gripper 11
#define GripperBase 0
#define Arm 6

//*******************************Defining objects*******************************
DualVNH5019MotorShield motors;
SharpIR SharpIR1(A12, 1080); // define input pin and model for SharpIR1
//SharpIR SharpIR2(A13, 1080); // define input pin and model for SharpIR2
// SharpIR1.distance();  // this returns the distance to the object
Adafruit_PWMServoDriver pwm = Adafruit_PWMServoDriver();

//*******************Variables definitions for line following*******************
const int base_speed = 90; // Speed of the motors at error 0
const int max_speed = 150; // Speed of the motors at max error

long sum_of = 0;
long avg = 0;
long sensor
[12] = {0, 0, 0, 0, 0, 0, 0, 0, 0, 0, 0, 0}; // A0-A11 analogRead store
long error = 0;
long last_error = 0;
long set_point = 750;
long pos = 0;
long proportional = 0;
long derivative = 0;
long error_value = 0;
long kp = 8;
long kd = 25;


void setup() {
  motors.init(); //PinMode setup for motors
  Serial.begin(9600); //enable communication with PC
  pwm.begin();
  pwm.setOscillatorFrequency(12000000);  // The int.osc. is closer to 27MHz
  pwm.setPWMFreq(SERVO_FREQ);  // Analog servos run at ~50 Hz updates
  delay(500);
}

void loop()
{
    Serial.println(SharpIR1.distance());
    if (SharpIR1.distance() == 16) {
      delay(250);
      if (SharpIR1.distance() == 16) {
        Serial.println(SharpIR1.distance());
        initializeArm();
        rotateBox();
        restArm();
      }
    }
  
//  error_value = pid_calculation() / 100;
//  // Serial.print(error_value);
//  // Serial.print(" ");
//  motors.setSpeeds(base_speed + error_value, base_speed - error_value);
//  //motor_driver(base_speed - error_value, base_speed + error_value);
  // Serial.print(base_speed - error_value);
  // Serial.print(" ");
  // Serial.print(base_speed + error_value);
  // Serial.println(" " );
  // delay(500);

}

//*****************************Function Definitions***************************//

//--------------------------Reading the IR sensor array-------------------------
int read_sensor() {
  long sum_of = 0;
  long avg = 0;
  long pos = 0;
  for (int i = 0; i < 12; i++) {
    sensor[i] = analogRead(i);
    if (sensor[i] < 100) sensor[i] = 1;
    else sensor[i] = 0;
  }
  for (int i = 0; i < 12; i++) {
    avg += sensor[i] * i * 100;
    sum_of += sensor[i];
    // Serial.print(sensor[i]); Serial.print(' ');
  }
  if (sum_of == 0) pos = set_point;
  else  pos = avg / sum_of;
  // Serial.print(avg); Serial.print(' ');
  // Serial.print(sum_of); Serial.print(' ')
  // Serial.println(pos); delay(1000);
  return pos; //Output of the read_sensor function.
}
//----------------------PID_calculation for line following----------------------
float pid_calculation() {
  error = read_sensor() - set_point;
  // Serial.println(error); delay(200);
  proportional = kp * error;
  // Serial.println(proportional); delay(200);
  derivative = kd * (error - last_error);
  last_error = error;
  error_value = proportional + derivative;
  return error_value;
  // Serial.println(error_value); delay(200);
}
// -----------------------Functions related to Robot arm------------------------
void initializeArm() {
  //Get the  arm to the initial position from wherever it was
  for (uint16_t microsec = 6000; microsec >= 2000; microsec--) pwm.writeMicroseconds(Arm, microsec); delay(1000);
  for (uint16_t microsec = 1000; microsec >= 400; microsec--) pwm.writeMicroseconds(Gripper, microsec); delay(500);
  for (uint16_t microsec = 3200; microsec >= 2500; microsec--) pwm.writeMicroseconds(GripperBase, microsec); delay(500);
  for (uint16_t microsec = 2000; microsec >= 400; microsec--) pwm.writeMicroseconds(Arm, microsec); delay(1000);
}

void rotateBox() {
  // Roate the box 90 degred toward the robot
  for (uint16_t microsec = 400; microsec <= 2200; microsec++) pwm.writeMicroseconds(Gripper, microsec); delay(500);
  for (uint16_t microsec = 400; microsec <= 2500; microsec++) pwm.writeMicroseconds(Arm, microsec); delay(500);
  for (uint16_t microsec = 2500; microsec <= 5500; microsec++) pwm.writeMicroseconds(GripperBase, microsec); delay(500);
  for (uint16_t microsec = 2500; microsec >= 2000; microsec--) pwm.writeMicroseconds(Arm, microsec); delay(500);
  for (uint16_t microsec = 2200; microsec >= 400; microsec--) pwm.writeMicroseconds(Gripper, microsec); delay(1000);
}

void restArm() {
  // Sending arm to the rest
  for (uint16_t microsec = 2000; microsec <= 6000; microsec++) pwm.writeMicroseconds(Arm, microsec); delay(500);
  for (uint16_t microsec = 1000; microsec >= 400; microsec--) pwm.writeMicroseconds(Gripper, microsec); delay(500);
  for (uint16_t microsec = 3200; microsec >= 2500; microsec--) pwm.writeMicroseconds(GripperBase, microsec); delay(500);
}

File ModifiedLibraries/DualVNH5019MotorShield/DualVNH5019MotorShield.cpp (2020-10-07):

#include "DualVNH5019MotorShield.h"

// Constructors ////////////////////////////////////////////////////////////////

DualVNH5019MotorShield::DualVNH5019MotorShield()
{
  //Pin map
  _INA1 = 22;
  _INB1 = 24;
  _PWM1 = 2;
  // _EN1DIAG1 = 6;
  // _CS1 = A0;
  _INA2 = 26;
  _INB2 = 28;
  _PWM2 = 3;
  // _EN2DIAG2 = 12;
  // _CS2 = A1;
}

DualVNH5019MotorShield::DualVNH5019MotorShield(unsigned char INA1,
                                               unsigned char INB1,
                                               unsigned char PWM1,
                                               unsigned char EN1DIAG1,
                                               unsigned char CS1,
                                               unsigned char INA2,
                                               unsigned char INB2,
                                               unsigned char PWM2,
                                               unsigned char EN2DIAG2,
                                               unsigned char CS2)
{
  _INA1 = INA1;
  _INB1 = INB1;
  _PWM1 = PWM1;
  _EN1DIAG1 = EN1DIAG1;
  _CS1 = CS1;
  _INA2 = INA2;
  _INB2 = INB2;
  _PWM2 = PWM2;
  _EN2DIAG2 = EN2DIAG2;
  _CS2 = CS2;
}

// Public Methods //////////////////////////////////////////////////////////////
void DualVNH5019MotorShield::init()
{
// Define pinMode for the pins and set the frequency for timer1.

  pinMode(_INA1,OUTPUT);
  pinMode(_INB1,OUTPUT);
  pinMode(_PWM1,OUTPUT);
  pinMode(_EN1DIAG1,INPUT);
  pinMode(_CS1,INPUT);
  pinMode(_INA2,OUTPUT);
  pinMode(_INB2,OUTPUT);
  pinMode(_PWM2,OUTPUT);
  pinMode(_EN2DIAG2,INPUT);
  pinMode(_CS2,INPUT);

  #ifdef DUALVNH5019MOTORSHIELD_TIMER1_AVAILABLE
    if (_PWM1 == _PWM1_TIMER1_PIN && _PWM2 == _PWM2_TIMER1_PIN)
    {
      // Timer 1 configuration
      // prescaler: clockI/O / 1
      // outputs enabled
      // phase-correct PWM
      // top of 400
      //
      // PWM frequency calculation
      // 16MHz / 1 (prescaler) / 2 (phase-correct) / 400 (top) = 20kHz
      TCCR1A = 0b10100000;
      TCCR1B = 0b00010001;
      ICR1 = 400;
    }
  #endif
}
// Set speed for motor 1, speed is a number betwenn -400 and 400
void DualVNH5019MotorShield::setM1Speed(int speed)
{
  unsigned char reverse = 0;

  if (speed < 0)
  {
    speed = -speed;  // Make speed a positive quantity
    reverse = 1;  // Preserve the direction
  }
  if (speed > 400)  // Max PWM dutycycle
    speed = 400;

  #ifdef DUALVNH5019MOTORSHIELD_TIMER1_AVAILABLE
    if (_PWM1 == _PWM1_TIMER1_PIN && _PWM2 == _PWM2_TIMER1_PIN)
    {
      OCR1A = speed;
    }
    else
    {
      analogWrite(_PWM1,speed * 51 / 80); // map 400 to 255
    }
  #else
    analogWrite(_PWM1,speed * 51 / 80); // map 400 to 255
  #endif

  if (speed == 0)
  {
    digitalWrite(_INA1,LOW);   // Make the motor coast no
    digitalWrite(_INB1,LOW);   // matter which direction it is spinning.
  }
  else if (reverse)
  {
    digitalWrite(_INA1,LOW);
    digitalWrite(_INB1,HIGH);
  }
  else
  {
    digitalWrite(_INA1,HIGH);
    digitalWrite(_INB1,LOW);
  }
}

// Set speed for motor 2, speed is a number betwenn -400 and 400
void DualVNH5019MotorShield::setM2Speed(int speed)
{
  unsigned char reverse = 0;

  if (speed < 0)
  {
    speed = -speed;  // make speed a positive quantity
    reverse = 1;  // preserve the direction
  }
  if (speed > 400)  // Max
    speed = 400;

  #ifdef DUALVNH5019MOTORSHIELD_TIMER1_AVAILABLE
    if (_PWM1 == _PWM1_TIMER1_PIN && _PWM2 == _PWM2_TIMER1_PIN)
    {
      OCR1B = speed;
    }
    else
    {
      analogWrite(_PWM2,speed * 51 / 80); // map 400 to 255
    }
  #else
    analogWrite(_PWM2,speed * 51 / 80); // map 400 to 255
  #endif

  if (speed == 0)
  {
    digitalWrite(_INA2,LOW);   // Make the motor coast no
    digitalWrite(_INB2,LOW);   // matter which direction it is spinning.
  }
  else if (reverse)
  {
    digitalWrite(_INA2,LOW);
    digitalWrite(_INB2,HIGH);
  }
  else
  {
    digitalWrite(_INA2,HIGH);
    digitalWrite(_INB2,LOW);
  }
}

// Set speed for motor 1 and 2
void DualVNH5019MotorShield::setSpeeds(int m1Speed, int m2Speed)
{
  setM1Speed(m1Speed);
  setM2Speed(m2Speed);
}

// Brake motor 1, brake is a number between 0 and 400
void DualVNH5019MotorShield::setM1Brake(int brake)
{
  // normalize brake
  if (brake < 0)
  {
    brake = -brake;
  }
  if (brake > 400)  // Max brake
    brake = 400;
  digitalWrite(_INA1, LOW);
  digitalWrite(_INB1, LOW);

  #ifdef DUALVNH5019MOTORSHIELD_TIMER1_AVAILABLE
    if (_PWM1 == _PWM1_TIMER1_PIN && _PWM2 == _PWM2_TIMER1_PIN)
    {
      OCR1A = brake;
    }
    else
    {
      analogWrite(_PWM1,brake * 51 / 80); // map 400 to 255
    }
  #else
    analogWrite(_PWM1,brake * 51 / 80); // map 400 to 255
  #endif
}

// Brake motor 2, brake is a number between 0 and 400
void DualVNH5019MotorShield::setM2Brake(int brake)
{
  // normalize brake
  if (brake < 0)
  {
    brake = -brake;
  }
  if (brake > 400)  // Max brake
    brake = 400;
  digitalWrite(_INA2, LOW);
  digitalWrite(_INB2, LOW);

  #ifdef DUALVNH5019MOTORSHIELD_TIMER1_AVAILABLE
    if (_PWM1 == _PWM1_TIMER1_PIN && _PWM2 == _PWM2_TIMER1_PIN)
    {
      OCR1B = brake;
    }
    else
    {
      analogWrite(_PWM2,brake * 51 / 80); // map 400 to 255
    }
  #else
    analogWrite(_PWM2,brake * 51 / 80); // map 400 to 255
  #endif
}

// Brake motor 1 and 2, brake is a number between 0 and 400
void DualVNH5019MotorShield::setBrakes(int m1Brake, int m2Brake)
{
  setM1Brake(m1Brake);
  setM2Brake(m2Brake);
}

/*
// Return motor 1 current value in milliamps.
unsigned int DualVNH5019MotorShield::getM1CurrentMilliamps()
{
  // 5V / 1024 ADC counts / 144 mV per A = 34 mA per count
  return analogRead(_CS1) * 34;
}

// Return motor 2 current value in milliamps.
unsigned int DualVNH5019MotorShield::getM2CurrentMilliamps()
{
  // 5V / 1024 ADC counts / 144 mV per A = 34 mA per count
  return analogRead(_CS2) * 34;
}

// Return error status for motor 1
unsigned char DualVNH5019MotorShield::getM1Fault()
{
  return !digitalRead(_EN1DIAG1);
}

// Return error status for motor 2
unsigned char DualVNH5019MotorShield::getM2Fault()
{
  return !digitalRead(_EN2DIAG2);
}
*/

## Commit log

2020-06-05 Renamed one file and add a new file
    Renamed How to choose a proper motor.pdf to Motor_Selection.pdf
    and add
    Power source selection.pdf
2020-06-05 Add modified version of Motor selection.pdf file
2020-06-05 Initiated motor driver sketch development
2020-06-05 Initiated servo driver sketch development
2020-06-06 Add solidworks simulation files.
    [1_Initial_prototype.SLDASM, 2_Motor_and_Wheel.SLDASM, 3_Robot_arm.SLDASM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]
2020-06-08 Added current status of the project to README.md
2020-06-11 Renamed SolidWorks_simulations into Solidworks_Models
    [1_Initial_prototype.SLDASM, 2_Motor_and_Wheel.SLDASM, 3_Robot_arm.SLDASM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]
2020-06-11 Changed a component in the initial prototype
    [1_Initial_prototype.SLDASM]
2020-06-12 Deleted Previous Models due to error
    [1_Initial_prototype.SLDASM, 2_Motor_and_Wheel.SLDASM, 3_Robot_arm.SLDASM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]
2020-06-12 Updated solidWorks Models
    [Arduino Mega Board.SLDPRT, Arduino Robot Arm 3D Model STEP File.SLDASM, Arm 01.sldprt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]
2020-09-22 Modified a SW model
    [Arduino Mega Board.SLDPRT, Attached part to platform.SLDPRT, Battety.SLDPRT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]
2020-09-22 Remove holes in Gripper base
    [Arduino Robot Arm 3D Model STEP File.SLDASM, Arm 01.sldprt, Arm 02 v3.sldprt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]
2020-09-24 made gripper base thicker and platform attachement hollow
    [Attached part to platform.SLDPRT, GRIPPER BASE.SLDPRT, GripperbaseNEW.SLDPRT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]
2020-09-24 finalized platforms and robot arm
    [Arduino Mega Board.SLDPRT, Attached part to platform.SLDPRT, Battety.SLDPRT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]
2020-09-26 Laser cut parts and their DXFs
    [ACT GEAR.DXF, ARM.DXF, BASE.DXF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]
2020-09-28 PCB designing initiated
    [Attached part to platform.SLDPRT, GRIPPER BASE.SLDPRT, RobotMAIN.PrjPcb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]
2020-09-28 Updated latest model
    [ROBO BRAND.SLDASM, ROBOT ARM SEMIFINAL REV1.SLDASM]
2020-10-01 Update lineFollowing.ino
    Update the line following code with 16 IR sensors
2020-10-01 motors are running
2020-10-03 Modified lateststable code and added STL files of the robot arm
    [ARM BASE.STL, Attached part to platform.SLDPRT, GRIPPER BASE.STL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]
2020-10-07 FIXED ERROR IN DRIVEN GEAR IN GRIPPER, add latest SW models
    [ACTUATING-GEAR.SLDPRT, DRIVEN-GEAR.SLDPRT, DRVN GEAR.DXF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]
2020-10-08 Add new SW part to attach power supply units
    [Power Supply base.DXF, Power Supply base.SLDPRT]
2020-10-09 Built the power distribution unit
    [GRIPPER BASE.SLDPRT, GRIPPER BASE2.STL]
2020-10-10 Order confirmed for 3d printing
2020-10-10 Add excel sheet of investments and expenses
    [Component List Robot Design.xlsx]
2020-10-10 Update excel sheet of investments and expenses
    [Component List Robot Design.xlsx]
2020-10-11 MPU 6050 gyroscope code
2020-10-11 Encoder Casing for POLOLU 25D motor
    The design is done through solid works.
    [RobotCap.SLDPRT, RobotCapNew.STL]
2020-10-11 Encoder code
    Not finalized yet. Still editing
2020-10-11 Encoder Final code
    80% done
2020-10-13 Major change to model: Change the arm base
    [ARMBASE--NEW--DXF.SLDPRT, ARMBASE--NEW.DXF, ArmBaseNew.SLDPRT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]
2020-10-15 Laser cut arm base, update inv and exp excel sheet
    [Component List Robot Design.xlsx]
2020-10-21 Robot arm code implementation initiated
2020-10-22 Robot arm basic motion implemented
2020-11-13 set the distance from the box to initialize the arm
2020-11-14 Update Encoder_final.ino
    included the whole code in 'drivedistance' function
2020-11-15 Update Encoder_final.ino
    declared left and right encoders seperately
2020-11-15 Update Encoder_final.ino
    Final code
2020-11-22 Robot arm checking 1
